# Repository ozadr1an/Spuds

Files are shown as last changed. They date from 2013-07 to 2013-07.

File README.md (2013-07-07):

Spuds
=====
**A Teensylu / Printrboard Mashup**
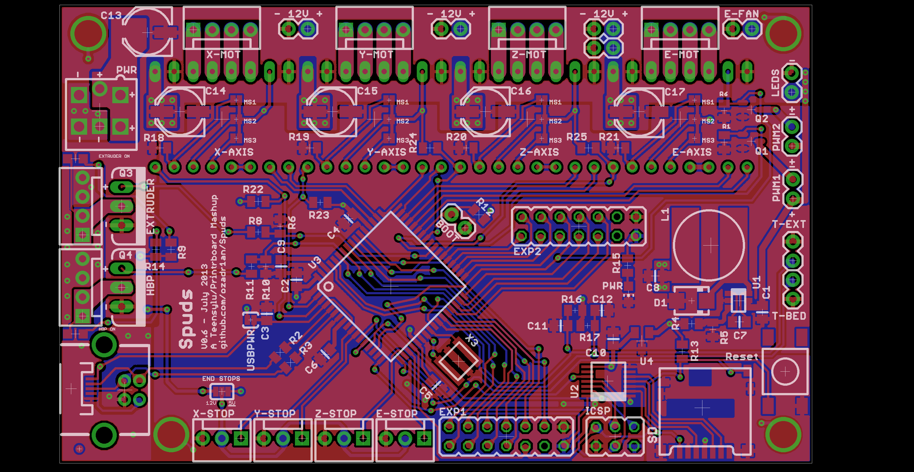
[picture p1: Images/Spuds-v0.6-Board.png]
Spuds-Board

Spuds was born from mashing together the concepts of both the Teensylu and Printrboard (itself a development of the Teensylu concept). The aim was to take the positives provided by the Printrboard design and incorporate some additions such as LED indicators on the MOSFETs, an additional PWM Fan header and an extra PWM Output header pin. It then reintroduced the modular Stepper Driver setup, as for many, the onboard Allegro drivers of the Printrboard are seen as a drawback as it limits options and replacement/repair. 

Spuds has expansion headers supporting I2C, SPI, UART, and ADC pins. All extra I/O ports of the AT90USB have been broken out to headers for prototyping and expansion. It follows the footprint for headers that the Printrboard introduced to allow compatibility with other expansions devices such as LCD's and the Extrudr board. 

The continued use of the AT90USB1286 used in the Teensylu and Printrboard means Spuds also has on-chip USB, removing the need for the FTDI UART (USB-to-serial) IC. On-chip USB means dramatically faster firmware upload times and communication. The AT90USB connects at any baud rate regardless of firmware configuration, and operates virtually free of serial communication errors/pauses.

This board is currently in pre-release design phases, so is subject to changes!

**Licence: _CC ShareAlike 3.0_**

**Attributions:**
* **_Teensylu_** (StephS 2011) http://reprap.org/wiki/Teensylu
* **_Printrboard_** (Laine Walker-Avina 2012) http://reprap.org/wiki/Printrboard

##Features
* Small design - board is 100mm x 60mm (4" x 2.4")
* Atmel AT90USB1286 Microcontroller (or AT90USB1287 drop-in compatible for 20mhz support)
 * Native USB interface. No FTDI serial-to-USB chip.
 * 128kb Flash
* Modular Stepper Driver Support (Add/Replace as needed)
* Solder Jumper Microstepping Selection
* Thermistor Connectivity: 2
* N-MOSFETs for Extruder and Heatbed control
 * LED Status Indicators for Power, HBP and Extruder (Troubleshooting, PID Monitoring)
* 2 N-MOSFET for low power Fan or motor
* 6 2-Pin Header 12V Connections for additional features such as LEDs, Cooling Fans, etc
* Onboard SD card slot
* Four Endstop connectors 
 * User selectable via Solder Jumpers 5V or 12v Rails.
 * Includes X, Y, Z, and fourth endstop called E-Stop to be used as an emergency stop, or extruder stop (to be added in firmware).
* Supports multiple power configurations (Carried from Sanguinololu)
 * Logic & Motors supplied by ATX or laptop power supply (12-20V 120W minimum)
 * Logic supplied by USB bus (if enabled by solder jumper)
 * Logic supplied by on-board voltage regulator
 * On-board USB connectivity
* Edge connectors enabling use of vertical or right-angle connections
* 15 Extra pins available for expansion and development, with the following capabilities
 * UART1 (RX and TX)
 * I2C (SDA and SCL)
 * SPI (MOSI, MISO, SCK)
 * PWM pin (2)
 * Analog I/O (6)
 * JTAG (uses some of the ADC pins)
 * Additional 14 pin header with remaining I/O for prototyping
 * SMT Components sized at 0805, and no QFNs for easier soldering.
 * 2-Layer PCB to reduce manufacture cost & complexity

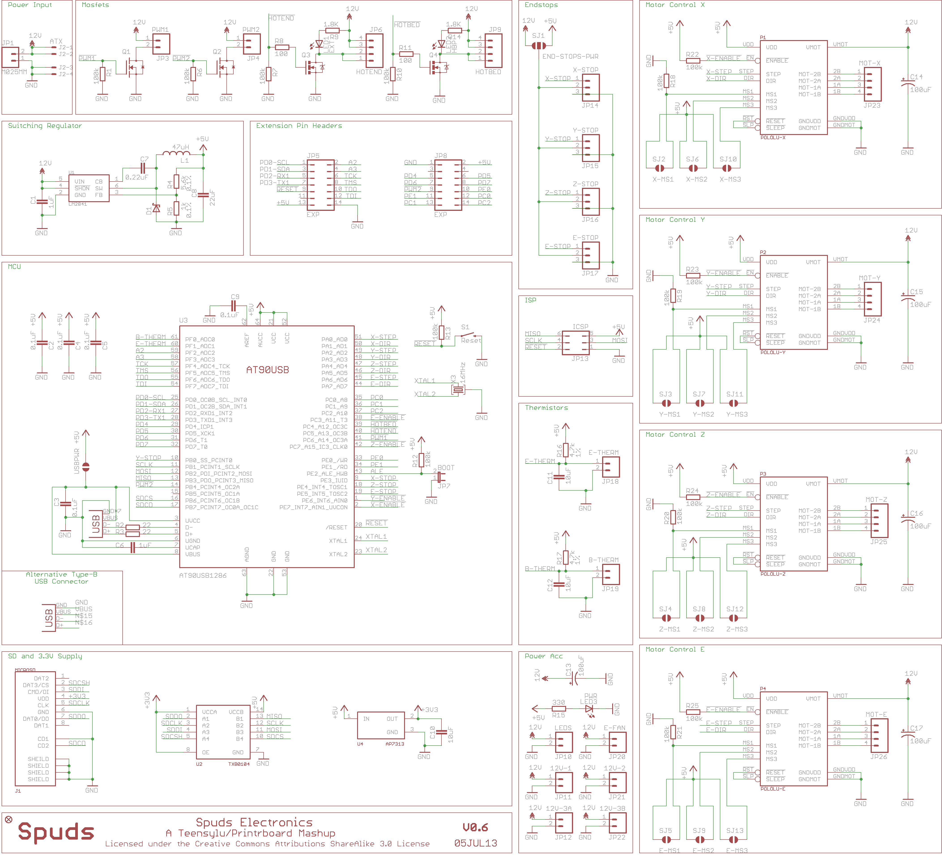
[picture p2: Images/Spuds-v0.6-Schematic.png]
Spuds-Schematic


####Benefits of this Design
* Allows modular use of Stepper Drivers, allowing:
 * User selection of driver used
 * The re-use of existing drivers
 * Replacement due to fault/failure.

* Integrated USB controller provides 12MBps bandwidth, instead of usual slower serial comms via FTDI. Result: Virtually no serial communication errors and interruptions due to PC Activity reduced.
* Integrated micro-SD Card slot
* Uses small standard Molex connectors for motors, heater, and endstops.

####Bill of Materials
Available via [GoogleDocs](https://docs.google.com/spreadsheet/ccc?key=0ArIeeziM0bp9dG5TbjlYaFVDQ0I5dkZXbHk2VjhtQlE&usp=sharing)

####Revision History
* V0.5 [July 2013]: Internal pre-production design.

####Compatible Firmwares
* Sprinter: http://reprap.org/wiki/Sprinter
* Marlin: No official support yet, but works with Lincomatic's fork (https://github.com/lincomatic/Marlin) or the Unofficial Solidoodle Firmware (https://github.com/mlaws/solidoodle2-marlin)
* Repetier List_of_Firmware#Repetier-Firmware: Supported, use MOTHERBOARD == 8. (https://github.com/repetier/Repetier-Firmware)
* grbl: No official support yet, but works with Lincomatic's fork. (http://blog.lincomatic.com/?p=564)

(Other firmwares are currently untested but any firmware for an arduino mega should work with proper pin setup.)

####Alternate Bootloader
If you have an ISP or JTAG cable, you can also program an alternate bootloader from the LUFA project that allows you to potentially program with the standard Arduino software.
* Download BootloaderCDC.zip
* Unzip to get BootloaderCDC.hex
* Program using your favorite ISP/JTAG cable.
 * The command for avrdude is avrdude -p at90usb1286 -c <your programmer here> -U flash:w:BootloaderCDC.hex

###Setup
####Stepper Motors
Connect the X, Y, Z axis, and extruder motors to the matching headers at the top of the Printrboard (X-MOT, Y-MOT, Z-MOT, E-MOT). Headers are 4 wire Molex KK series, part# 0022013047) with 2759 series crimp terminals, part# 0008550101. Motor pinout is:
1. A - Phase 1+
2. B - Phase 1-
3. C - Phase 2+
4. D - Phase 2-

####Endstops
Connect mechanical microswitches to the 3-pin Molex headers X-STOP, Y-STOP, Z-STOP at the bottom of the board. E-STOP is reserved for future use. Connect switches as follows:
#####Standard Microswitches
1. Switch NC
2. No connection
3. Switch COMMON

#####For optos:
1. Signal Output
2. +5V or +12V
3. GND

####Heaters
* LEDs are fitted to indicate when the MOSFET is active. These can be ommitted if desired. 
* Connect the heating element of your hotend (resistor or nichrome wire) to the 4-pin EXTRUDER header, positioned next to MOSFET Q1. 
* Connect your heatbed to the HOTBED header, next to MOSFET Q2. Polarity here is unimportant; pinout is as follows:

1. Positive
2. Positive
3. Negative
4. Negative

####Thermistors
Thermistor headers are 2-pin Molex headers at the right side of the board, located above the reset button.
* Connect the HBP thermistor to the header directly above the reset button. 
* The Extruder thermistor also connects above the reset button next to the HBP thermistor.

####Low Power Fan
A 2-pin Molex header labelled FAN is located on the right side of the board, above the thermistor headers. 
* This optional header can be used to power a fan or other small motor.

####Board Power
All power is supplied through a choice of connector at the upper left corner of the Spuds, labelled PWR:
* 4-pin ATX style header (Suitable for high current HBP)
* 5.08mm 2-Pin Screw Terminal (Suitable for low current HBP only)

Connect directly to any 12VDC power supply. 
* Ground terminals are closest to the edge of the board
* 12VDC+ terminals are located behind.

####USB
Choice of USB Connector (only one can be installed). The Type-B connector is a good choice for long cable runs, as you can easily acquire heavily sheilded thick gauge USB cables as used for Printers. Micro-USB is perhaps a good choice if a small compact connection is required, or for interconnection to another controller system such as a tablet or RPi:
* Micro-USB B Connector
* Type-B USB Connector

**Note that a jumper should _NOT_ be installed on the "BOOT" pins for normal operation (see _Bootloaders_ ).**

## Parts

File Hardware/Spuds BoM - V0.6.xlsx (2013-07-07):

Qty | Value | Device | Board Ref. | Digikey p/n | Unit Price | Total Part Price
1 | TXB0104 | TXB0104 Bi-Di Level Translator | U2 | 296-21929-1-ND | 0.743 | $0.74
1 | AP7313 | AP7313 3.3V LDO SOT-23 | U4 | AP7313-33SAG-7DICT-ND | 0.112 | $0.11
1 | AT90USB1286-AU | AT90USB | U3 | AT90USB1286-AURCT-ND | 6.14 | $6.14
1 | LM2841 | LM2841 Switching Regulator | U1 | LM2841XMK-ADJLCT-ND | 1.596 | $1.60
1 | BOOT | 0.1” 2-PIN MALE HEADER | JP7 | WM4000-ND | 0.063 | $0.06
2 | EXP | 0.1” 2X7 MALE PIN HEADER | JP5, JP8 | 609-3491-ND | 0.14166 | $0.28
1 | ICSP | 0.1” 2X3 MALE PIN HEADER | JP13 | 609-3210-ND | 0.29275 | $0.29
7 | LEDS/12V | 0.1” 2-PIN MALE HEADER | JP3, JP4, JP11, JP21, JP12, JP22, JP20 | WM4000-ND | 0.063 | $0.44
6 | MOTOR | 4-PIN 0.1” POLARIZED MOLEX KK-SERIES | JP6, JP9, JP23, JP24, JP25, JP26 | WM4113-ND | 0.17596 | $1.06
2 | THERM | 2-PIN 0.1” POLARIZED MOLEX KK-SERIES | JP18, JP19 | WM4111-ND | 0.09237 | $0.18
4 | ENDSTOP | 3-PIN 0.1” POLARIZED MOLEX KK-SERIES | JP14, JP15, JP16, JP17 | WM4112-ND | 0.13541 | $0.54
2 | POLOLU-SOCKET | CONN HEADER 32POS SOCKET 2.54MM |  | 732-2860-ND | 1.34 | $2.68
1 | MICROSD | MICROSD Socket, Amphenol | J1 | 114-00841-68-1-ND | 0.856 | $0.86
1 | USB-PTH-B | CONN USB TYPE B R/A BLACK | X2 | ED2983-ND | 0.54 | $0.54
0 | USB-MICROB | USB-MICROB | X1 | 455-2562-1-ND | 0.5355 | $0.00
0 | PWR | TERM BLOCK 2POS SIDE ENTRY 5MM | JP1 | A98355-ND | 0.87 | $0.00
1 | ATX | Molex Mini-Fit Jr. 5566-4 | J3 | WM3801-ND | 0.33582 | $0.34
1 | 20MHz | RESONATOR W/ INTEGRATED CAP | X3 | 535-10011-1-ND | 0.45 | $0.45
0 | 16MHz | RESONATOR W/ INTEGRATED CAP | X3 | 535-10008-2-ND | 0.182 | $0.00
5 | 0.1uF | CAPACITOR CERAMIC 0805 | C2, C3, C4, C5, C9 | 311-1361-1-ND | 0.006 | $0.03
1 | 0.22uF | CAPACITOR CERAMIC 0805 | C7 | 399-3491-1-ND | 0.02043 | $0.02
2 | 1uF | CAPACITOR CERAMIC 0805 | C1, C6 | 587-2229-1-ND | 0.03055 | $0.06
3 | 10uF | CAPACITOR CERAMIC 0805 | C10, C11, C12 | 311-1355-1-ND | 0.025 | $0.07
1 | 22uF | CAPACITOR CERAMIC 0805 | C8 | 587-1305-1-ND | 0.056 | $0.06
5 | 100uF | CAP, Al Electrolytic, Panasonic-D Pkg | C13, C14, C15, C16, C17 | PCE3951CT-ND | 0.1202 | $0.60
1 |  | DIODE SCHOTTKY 40V 1A SMA | D1 | B140-FDICT-ND | 0.0648 | $0.06
1 | 47uH | Inductor, SMT 1.25A | L1 | SDR1006-470KLCT-ND | 0.3 | $0.30
3 | PWR | LED GREEN 0805 | LED1, LED2, LED3 | 754-1131-1-ND | 0.039 | $0.12
2 |  | Logic-level n-Chan MOSFET SOT-23 | Q1, Q2 | IRLML2060TRPBFCT-ND | 0.087 | $0.17
2 |  | Logic-level n-Chan MOSFET TO-220 | Q3, Q4 | IRLB8743PBF-ND | 0.52632 | $1.05
1 | 1k | RESISTOR_0805 0.1% | R5 | RG20P1.0KBCT-ND | 0.058 | $0.06
2 | 1.8k | RESISTOR_0805 | R9, R14 | 311-1.8LHCT-ND | 0.058 | $0.12
2 | 4.7k | RESISTOR_0805 1% | R16, R17 | 311-4.70KCRCT-ND | 0.00266 | $0.01
1 | 5.6k | RESISTOR_0805 0.1% | R4 | P5.6KDATR-ND | 0.013 | $0.01
2 | 22 | RESISTOR_0805 | R2, R3 | 311-22ARCT-ND | 0.00209 | $0.00418
2 | 100 | RESISTOR_0805 | R8, R11 | 311-100ARCT-ND | 0.00209 | $0.00418
14 | 100k | RESISTOR_0805 | R1, R6, R7, R10, R12, R13, R18, R19, R20, R21, R22, R23, R24, R25 | RMCF0805JT100KCT-ND | 0.0019 | $0.03
1 | 330 | RESISTOR_0805 | R15 | 311-330ARCT-ND | 0.00209 | $0.00209
1 | Reset | SWITCH-MOMENTARY-2 | S2 | 450-1133-ND | 0.1398 | $0.14
 |  |  |  |  | Total: | $19.24

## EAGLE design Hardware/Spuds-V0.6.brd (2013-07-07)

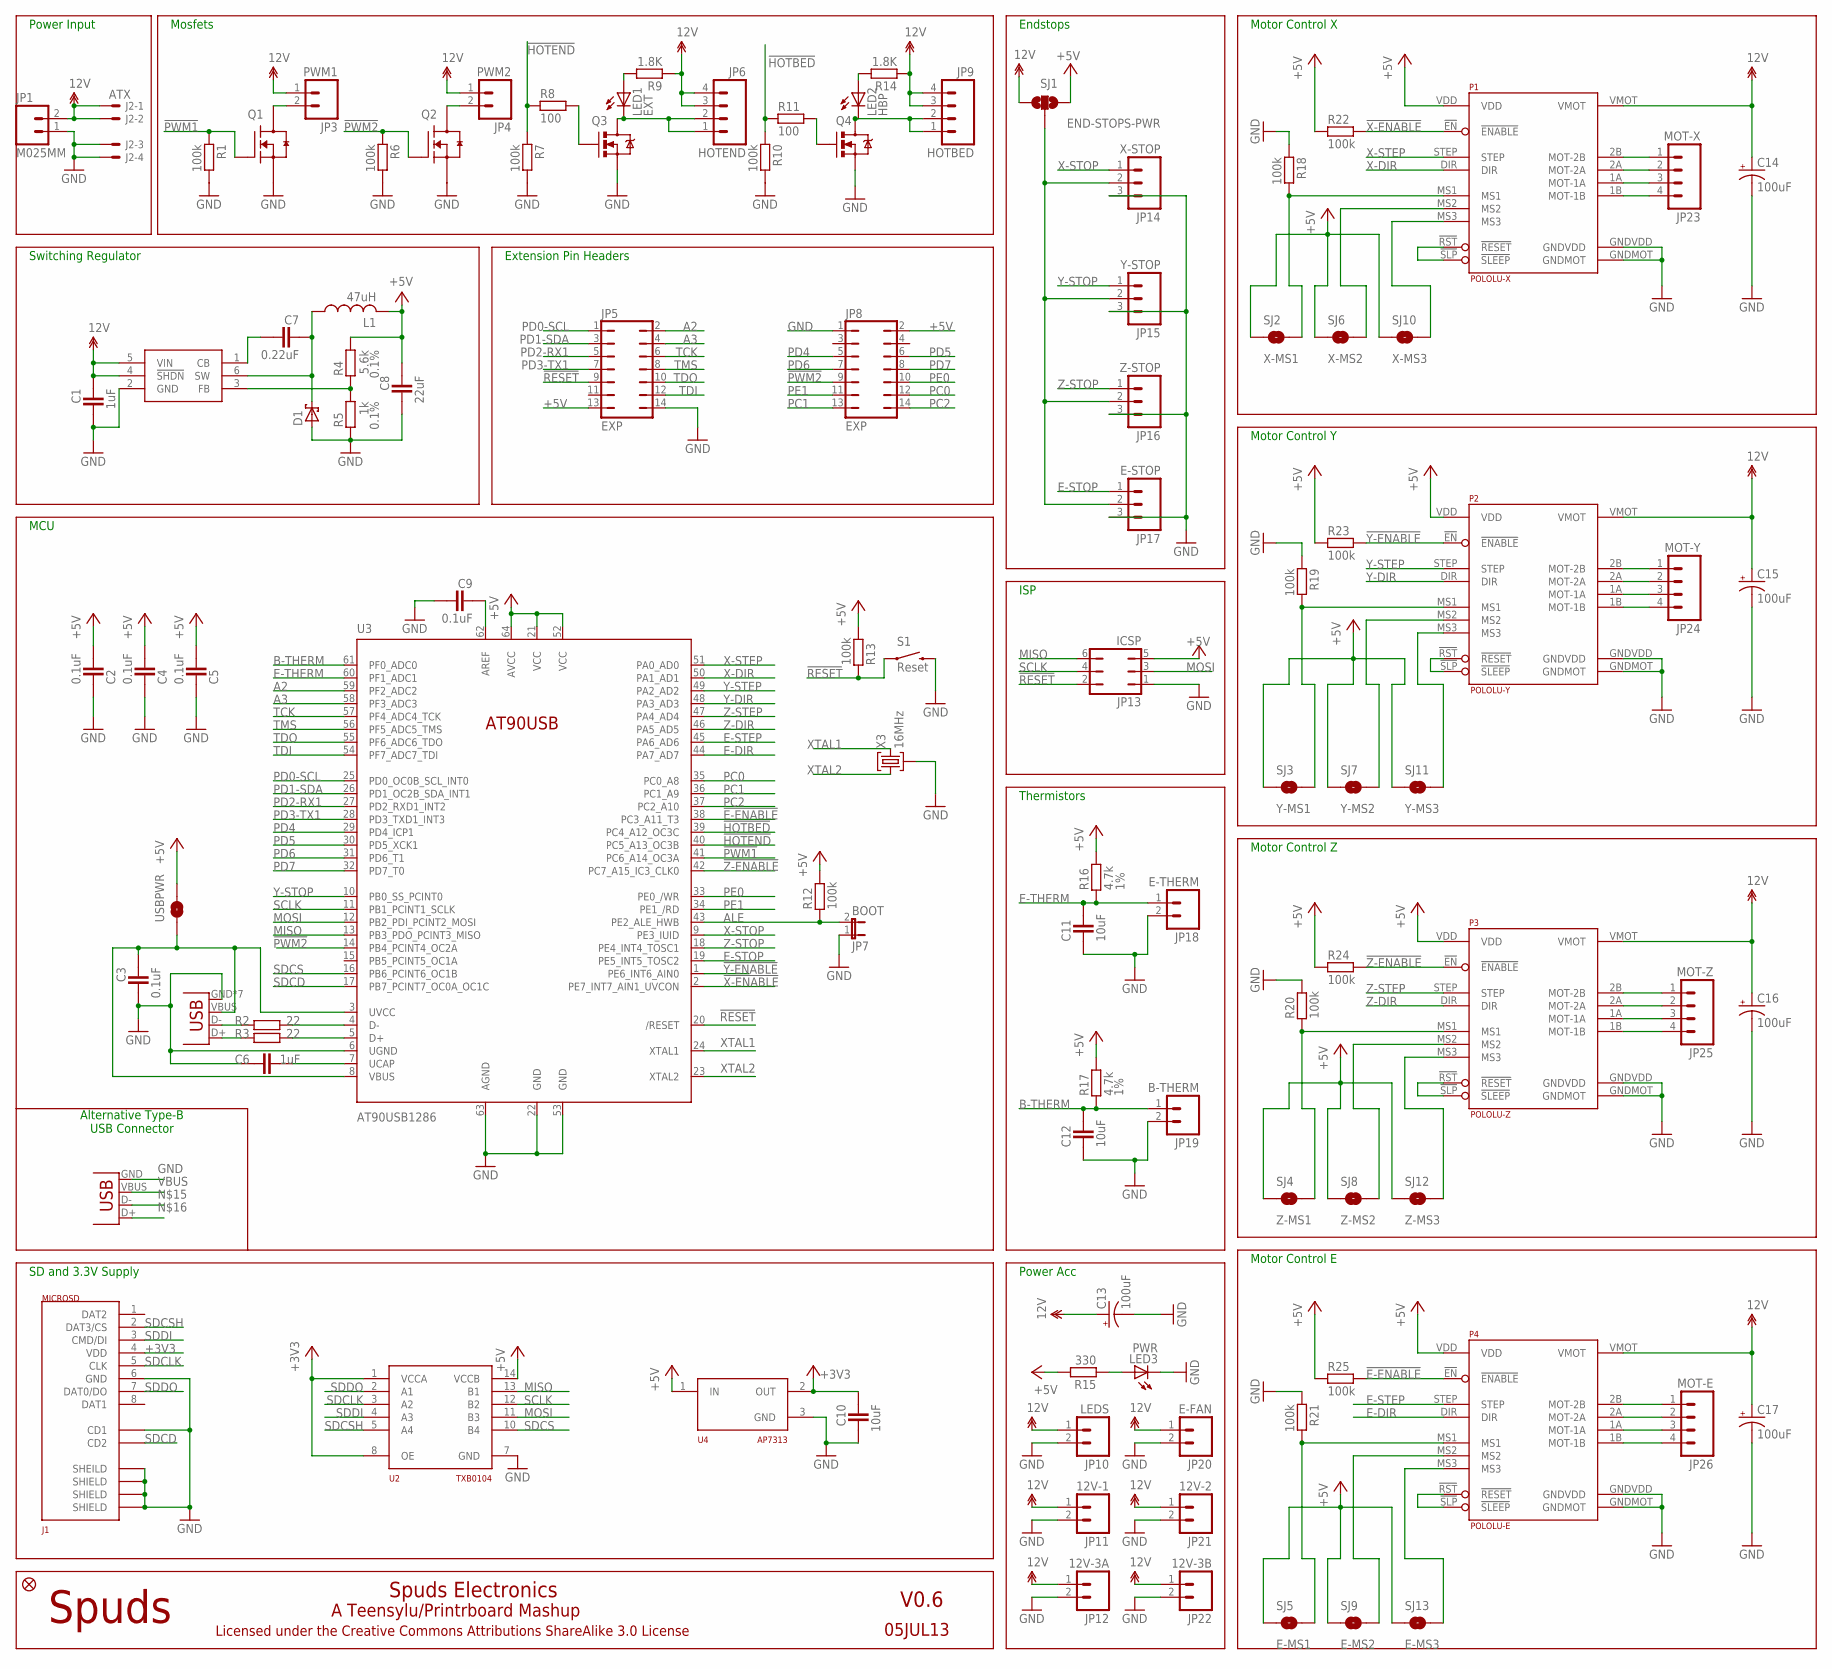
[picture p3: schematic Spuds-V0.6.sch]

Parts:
C1, C6: 1uF; CAPC2012X145AN; PARTNO 587-2229-1-ND
C2, C3, C4, C5, C9: 0.1uF; CAPC2012X145AN; PARTNO 311-1361-1-ND
C7: 0.22uF; CAPC2012X145AN; PARTNO 399-3491-1-ND
C8: 22uF; CAPC2012X145AN; PARTNO 587-1305-1-ND
C10, C11, C12: 10uF; CAPC2012X145AN; PARTNO 311-1355-1-ND
C13, C14, C15, C16, C17: 100uF; PANASONIC_D; PARTNO PCE3951CT-ND
D1: SCH-DIODESMA; SMA; PARTNO B140-FDICT-ND
J1: MICROSD; AMPHENOL-MICROSD; PARTNO ED2983-ND
J2: ATX; 5566-4; PARTNO WM3801-ND
JP1: M025MM; SCREWTERMINAL-5MM-2; PARTNO A98355-ND
JP2: FIDUCIAL1X2.5; FIDUCIAL-1X2.5; PARTNO *
JP3: PWM1; 1X02; PARTNO WM4000-ND
JP4: PWM2; 1X02; PARTNO WM4000-ND
JP5, JP8: EXP; JP7Q; PARTNO 609-3491-ND
JP6: HOTEND; MOLEX-1X4; PARTNO WM4113-ND
JP7: BOOT; 1X02; PARTNO WM4000-ND
JP9: HOTBED; MOLEX-1X4; PARTNO WM4113-ND
JP10: LEDS; 1X02; PARTNO WM4000-ND
JP11: 12V-1; 1X02; PARTNO WM4111-ND
JP12: 12V-3A; 1X02; PARTNO WM4111-ND
JP13: ICSP; JP3Q; PARTNO 609-3210-ND
JP14: X-STOP; MOLEX-1X3; PARTNO WM4112-ND
JP15: Y-STOP; MOLEX-1X3; PARTNO WM4112-ND
JP16: Z-STOP; MOLEX-1X3; PARTNO WM4112-ND
JP17: E-STOP; MOLEX-1X3; PARTNO WM4112-ND
JP18: E-THERM; 1X02; PARTNO WM4111-ND
JP19: B-THERM; 1X02; PARTNO WM4111-ND
JP20: E-FAN; 1X02; PARTNO WM4111-ND
JP21: 12V-2; 1X02; PARTNO WM4111-ND
JP22: 12V-3B; 1X02; PARTNO WM4111-ND
JP23: MOT-X; MOLEX-1X4; PARTNO WM4113-ND
JP24: MOT-Y; MOLEX-1X4; PARTNO WM4113-ND
JP25: MOT-Z; MOLEX-1X4; PARTNO WM4113-ND
JP26: MOT-E; MOLEX-1X4; PARTNO WM4113-ND
L1: 47uH; SDR1006; PARTNO SDR1006-470KLCT-ND
LED1: EXT; CHIP-LED0805; PARTNO 754-1132-1-ND
LED2: HBP; CHIP-LED0805; PARTNO 754-1437-1-ND
LED3: PWR; CHIP-LED0805; PARTNO 754-1131-1-ND
P1: POLOLU-X; POLOLU-ALLEGRO-PTH; PARTNO 952-1823-ND
P2: POLOLU-Y; POLOLU-ALLEGRO-PTH; PARTNO 952-1823-ND
P3: POLOLU-Z; POLOLU-ALLEGRO-PTH; PARTNO 952-1823-ND
P4: POLOLU-E; POLOLU-ALLEGRO-PTH; PARTNO 952-1823-ND
Q1, Q2: RFP30N06LE; SOT95P280X135-3N; PARTNO IRLML2060TRPBFCT-ND
Q3, Q4: RFP30N06LE; TO220V; PARTNO IRLB8743PBF-ND
R1, R6, R7, R10, R12, R13, R18, R19, R20, R21, R22, R23, R24, R25: 100k; RESC2012X70N; PARTNO RMCF0805JT100KCT-ND
R2, R3: 22; RESC2012X70N; PARTNO 311-22ARCT-ND
R4: 5.6k; RESC2012X70N; TOLERANCE 0.1%; PARTNO P5.6KDATR-ND
R5: 1k; RESC2012X70N; TOLERANCE 0.1%; PARTNO RG20P1.0KBCT-ND
R8, R11: 100; RESC2012X70N; PARTNO 311-100ARCT-ND
R9, R14: 1.8K; RESC2012X70N; PARTNO 311-1.8LHCT-ND
R15: 330; RESC2012X70N; PARTNO 311-330ARCT-ND
R16, R17: 4.7k; RESC2012X70N; TOLERANCE 1%; PARTNO 311-4.70KCRCT-ND
S1: Reset; TACTILE_SWITCH_TALL; PARTNO 450-1133-ND
SJ1: END-STOPS-PWR; SJ_3_PASTE2&3; PARTNO *
SJ2: X-MS1; SJ_2S; PARTNO *
SJ3: Y-MS1; SJ_2S; PARTNO *
SJ4: Z-MS1; SJ_2S; PARTNO *
SJ5: E-MS1; SJ_2S; PARTNO *
SJ6: X-MS2; SJ_2S; PARTNO *
SJ7: Y-MS2; SJ_2S; PARTNO *
SJ8: Z-MS2; SJ_2S; PARTNO *
SJ9: E-MS2; SJ_2S; PARTNO *
SJ10: X-MS3; SJ_2S; PARTNO *
SJ11: Y-MS3; SJ_2S; PARTNO *
SJ12: Z-MS3; SJ_2S; PARTNO *
SJ13: E-MS3; SJ_2S; PARTNO *
U1: LM2841; TSOT6; PARTNO LM2841XMK-ADJLCT-ND
U2: TXB0104; TSSOP14; PARTNO 296-21929-1-ND
U3: AT90USB1286; TQFP64-2; PARTNO AT90USB1286-AURCT-ND
U4: AP7313; SOT23C; PARTNO AP7313-33SAG-7DICT-ND
USBPWR: SOLDERJUMPERNO; SJ_2S-NO; PARTNO *
X1: USBPTH; USB-B-PTH; PARTNO ED2983-ND
X2: USB-MICROB; PARTNO 455-2562-1-ND
X3: 16MHz; AWSCR; PARTNO 535-10011-1-ND

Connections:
12V: C1.1, C13.+, C14.+, C15.+, C16.+, C17.+, J2.1, J2.2, JP1.2, JP3.1, JP4.1, JP6.3, JP6.4, JP9.3, JP9.4, JP10.1, JP11.1, JP12.1, JP20.1, JP21.1, JP22.1, P1.VMOT, P2.VMOT, P3.VMOT, P4.VMOT, R9.1, R14.1, SJ1.1, U1.4 (!SHDN), U1.5 (VIN)
!E-ENABLE: P4.!EN (!ENABLE), R25.2, U3.38 (PC3_A11_T3)
!HOTBED: R10.1, R11.1, U3.39 (PC4_A12_OC3C)
!HOTEND: R7.1, R8.1, U3.40 (PC5_A13_OC3B)
!PWM1: Q1.1 (G), R1.1, U3.41 (PC6_A14_OC3A)
!PWM2: JP8.9, Q2.1 (G), R6.1, U3.14 (PB4_PCINT4_OC2A)
!RESET: JP5.9, JP13.2, R13.1, S1.A2 (1), U3.20 (/RESET)
!X-ENABLE: P1.!EN (!ENABLE), R22.2, U3.2 (PE7_INT7_AIN1_UVCON)
!Y-ENABLE: P2.!EN (!ENABLE), R23.2, U3.1 (PE6_INT6_AIN0)
!Z-ENABLE: P3.!EN (!ENABLE), R24.2, U3.42 (PC7_A15_IC3_CLK0)
+3V3: C10.1, J1.4 (VDD), U2.1 (VCCA), U2.8 (OE), U4.2 (OUT)
+5V: C2.2, C4.2, C5.2, C8.1, JP5.13, JP8.2, JP13.5, L1.P$2 (2), P1.VDD, P2.VDD, P3.VDD, P4.VDD, R4.1, R12.2, R13.2, R15.2, R16.2, R17.2, R22.1, R23.1, R24.1, R25.1, SJ1.3, SJ2.1, SJ3.1, SJ4.1, SJ5.1, SJ6.1, SJ7.1, SJ8.1, SJ9.1, SJ10.1, SJ11.1, SJ12.1, SJ13.1, U2.14 (VCCB), U3.21 (VCC), U3.52 (VCC), U3.64 (AVCC), U4.1 (IN), USBPWR.2
A2: JP5.2, U3.59 (PF2_ADC2)
A3: JP5.4, U3.58 (PF3_ADC3)
ALE: JP7.2, R12.1, U3.43 (PE2_ALE_HWB)
AREF: C9.1, U3.62 (AREF)
B-THERM: C12.2, JP19.1, R17.1, U3.61 (PF0_ADC0)
E-DIR: P4.DIR, U3.44 (PA7_AD7)
E-MS1: P4.MS1, R21.2, SJ5.2
E-MS2: P4.MS2, SJ9.2
E-MS3: P4.MS3, SJ13.2
E-RESETSLEEP: P4.!RST (!RESET), P4.!SLP (!SLEEP)
E-STEP: P4.STEP, U3.45 (PA6_AD6)
E-STOP: JP17.1, U3.19 (PE5_INT5_TOSC2)
E-THERM: C11.2, JP18.1, R16.1, U3.60 (PF1_ADC1)
END-STOP-PWR: JP14.2, JP15.2, JP16.2, JP17.2, SJ1.2
GND: C1.2, C2.1, C3.2, C4.1, C5.1, C6.1, C8.2, C9.2, C10.2, C11.1, C12.1, C13.-, C14.-, C15.-, C16.-, C17.-, D1.A, J1.6 (GND), J1.C1 (SHEILD), J1.C2 (SHIELD), J1.C3 (SHIELD), J1.C4 (SHIELD), J1.CD1, J2.3, J2.4, JP1.1, JP5.14, JP7.1, JP8.1, JP10.2, JP11.2, JP12.2, JP13.1, JP14.3, JP15.3, JP16.3, JP17.3, JP18.2, JP19.2, JP20.2, JP21.2, JP22.2, LED3.C, P1.GNDMOT, P1.GNDVDD, P2.GNDMOT, P2.GNDVDD, P3.GNDMOT, P3.GNDVDD, P4.GNDMOT, P4.GNDVDD, Q1.2 (S), Q2.2 (S), Q3.3 (S), Q4.3 (S), R1.2, R5.2, R6.2, R7.2, R10.2, R18.1, R19.1, R20.2, R21.1, S1.B2 (2), U1.2 (GND), U2.7 (GND), U3.6 (UGND), U3.22 (GND), U3.53 (GND), U3.63 (AGND), U4.3 (GND), X1.GND, X2.GND, X2.MT1 (GND), X2.MT2 (GND), X2.MT3 (GND), X2.MT4 (GND), X2.MT5 (GND), X2.MT6 (GND), X3.GND (2)
HOTBED-GND: JP9.1, JP9.2, LED2.C, Q4.2 (D)
HOTEND-GND: JP6.1, JP6.2, LED1.C, Q3.2 (D)
MISO: JP13.6, U2.13 (B1), U3.13 (PB3_PDO_PCINT3_MISO)
MOSI: JP13.3, U2.11 (B3), U3.12 (PB2_PDI_PCINT2_MOSI)
unnamed: LED3.A, R15.1
unnamed: LED1.A, R9.2
unnamed: R2.2, U3.4 (D-)
unnamed: R3.2, U3.5 (D+)
unnamed: LED2.A, R14.2
unnamed: JP3.2, Q1.3 (D)
unnamed: Q4.1 (G), R11.2
unnamed: JP24.2, P2.2A (MOT-2A)
unnamed: C6.2, U3.7 (UCAP)
unnamed: JP23.1, P1.2B (MOT-2B)
unnamed: JP23.2, P1.2A (MOT-2A)
unnamed: JP23.3, P1.1A (MOT-1A)
unnamed: JP23.4, P1.1B (MOT-1B)
unnamed: JP4.2, Q2.3 (D)
unnamed: R2.1, X1.D-, X2.D-
unnamed: R3.1, X1.D+, X2.D+
unnamed: R4.2, R5.1, U1.3 (FB)
unnamed: JP24.3, P2.1A (MOT-1A)
unnamed: JP24.4, P2.1B (MOT-1B)
unnamed: JP24.1, P2.2B (MOT-2B)
unnamed: JP26.1, P4.2B (MOT-2B)
unnamed: JP26.2, P4.2A (MOT-2A)
unnamed: JP26.3, P4.1A (MOT-1A)
unnamed: JP26.4, P4.1B (MOT-1B)
unnamed: Q3.1 (G), R8.2
unnamed: C7.1, D1.C, L1.P$1 (1), U1.6 (SW)
unnamed: C7.2, U1.1 (CB)
PC0: JP8.12, U3.35 (PC0_A8)
PC1: JP8.13, U3.36 (PC1_A9)
PC2: JP8.14, U3.37 (PC2_A10)
PD0-SCL: JP5.1, U3.25 (PD0_OC0B_SCL_INT0)
PD1-SDA: JP5.3, U3.26 (PD1_OC2B_SDA_INT1)
PD2-RX1: JP5.5, U3.27 (PD2_RXD1_INT2)
PD3-TX1: JP5.7, U3.28 (PD3_TXD1_INT3)
PD4: JP8.5, U3.29 (PD4_ICP1)
PD5: JP8.6, U3.30 (PD5_XCK1)
PD6: JP8.7, U3.31 (PD6_T1)
PD7: JP8.8, U3.32 (PD7_T0)
PE0: JP8.10, U3.33 (PE0_/WR)
PE1: JP8.11, U3.34 (PE1_/RD)
SCLK: JP13.4, U2.12 (B2), U3.11 (PB1_PCINT1_SCLK)
SDCD: J1.CD2, U3.17 (PB7_PCINT7_OC0A_OC1C)
SDCLK: J1.5 (CLK), U2.3 (A2)
SDCS: U2.10 (B4), U3.16 (PB6_PCINT6_OC1B)
SDCSH: J1.2 (DAT3/CS), U2.5 (A4)
SDDI: J1.3 (CMD/DI), U2.4 (A3)
SDDO: J1.7 (DAT0/DO), U2.2 (A1)
TCK: JP5.6, U3.57 (PF4_ADC4_TCK)
TDI: JP5.12, U3.54 (PF7_ADC7_TDI)
TDO: JP5.10, U3.55 (PF6_ADC6_TDO)
TMS: JP5.8, U3.56 (PF5_ADC5_TMS)
VBUS: C3.1, U3.3 (UVCC), U3.8 (VBUS), USBPWR.1, X1.VBUS, X2.VBUS
X-DIR: P1.DIR, U3.50 (PA1_AD1)
X-MS1: P1.MS1, R18.2, SJ2.2
X-MS2: P1.MS2, SJ6.2
X-MS3: P1.MS3, SJ10.2
X-RESETSLEEP: P1.!RST (!RESET), P1.!SLP (!SLEEP)
X-STEP: P1.STEP, U3.51 (PA0_AD0)
X-STOP: JP14.1, U3.9 (PE3_IUID)
XTAL1: U3.24 (XTAL1), X3.IN (3)
XTAL2: U3.23 (XTAL2), X3.OUT (1)
Y-DIR: P2.DIR, U3.48 (PA3_AD3)
Y-MS1: P2.MS1, R19.2, SJ3.2
Y-MS2: P2.MS2, SJ7.2
Y-MS3: P2.MS3, SJ11.2
Y-RESETSLEEP: P2.!RST (!RESET), P2.!SLP (!SLEEP)
Y-STEP: P2.STEP, U3.49 (PA2_AD2)
Y-STOP: JP15.1, U3.10 (PB0_SS_PCINT0)
Z-DIR: P3.DIR, U3.46 (PA5_AD5)
Z-MOT-1A: JP25.3, P3.1A (MOT-1A)
Z-MOT-1B: JP25.4, P3.1B (MOT-1B)
Z-MOT-2A: JP25.2, P3.2A (MOT-2A)
Z-MOT-2B: JP25.1, P3.2B (MOT-2B)
Z-MS1: P3.MS1, R20.1, SJ4.2
Z-MS2: P3.MS2, SJ8.2
Z-MS3: P3.MS3, SJ12.2
Z-RESETSLEEP: P3.!RST (!RESET), P3.!SLP (!SLEEP)
Z-STEP: P3.STEP, U3.47 (PA4_AD4)
Z-STOP: JP16.1, U3.18 (PE4_INT4_TOSC1)

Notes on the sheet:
Motor Control X
Motor Control Y
Motor Control Z
Motor Control E
ISP
Thermistors
Endstops
Mosfets
Power Acc
Spuds
V0.6
Spuds Electronics
Licensed under the Creative Commons Attributions ShareAlike 3.0 License
Extension Pin Headers
Switching Regulator
A Teensylu/Printrboard Mashup
SD and 3.3V Supply
Power Input
MCU
Alternative Type-B USB Connector
05JUL13

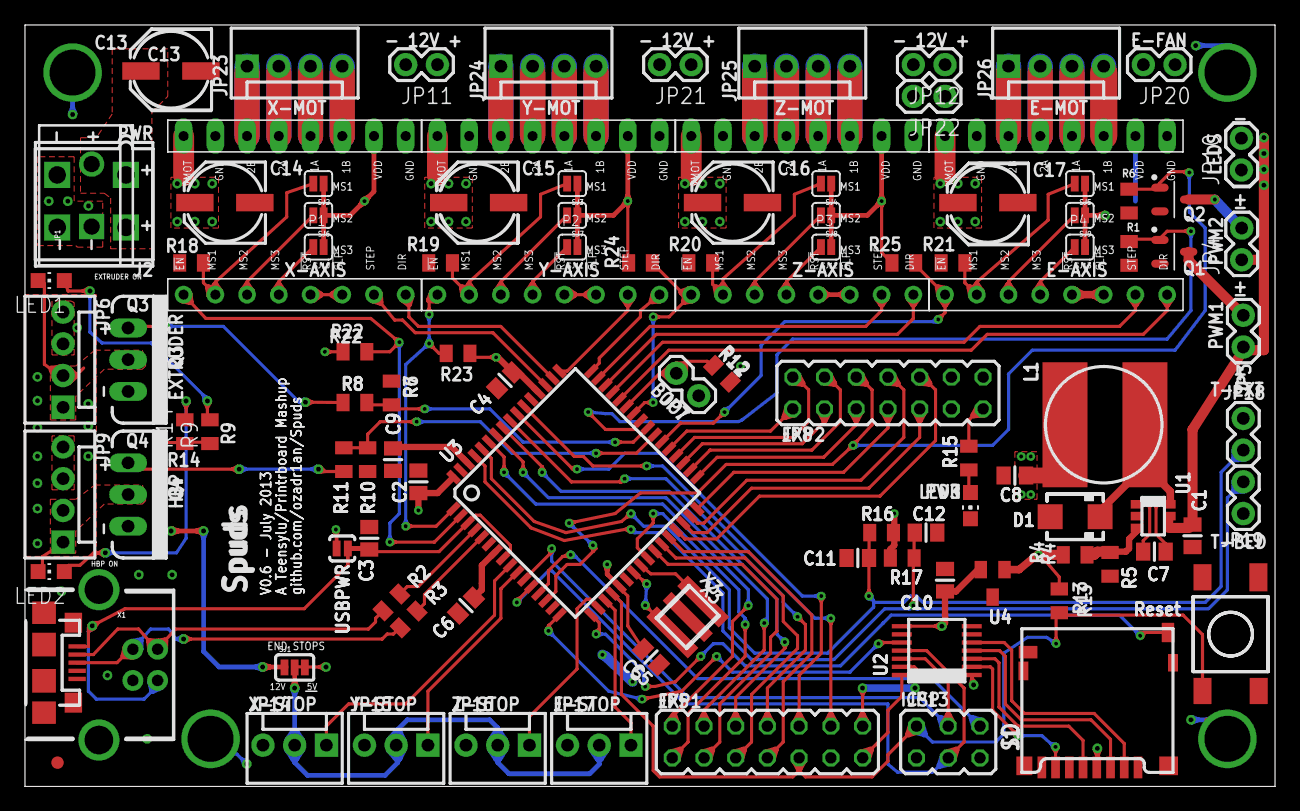
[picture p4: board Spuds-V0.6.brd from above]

Board: 4 copper layers, 100.1 x 61.0 mm, 106 parts (0 on the bottom side), 110 nets.

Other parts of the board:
DRILEGEND: DRILEGEND

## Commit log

2013-07-07 Initial Schematic/Board Commit V0.6 BoM
    [Spuds BoM - V0.6.xlsx, Spuds-V0.6.brd, Spuds-V0.6.sch]
2013-07-07 Update README.md
    Added Board/Schematic Images

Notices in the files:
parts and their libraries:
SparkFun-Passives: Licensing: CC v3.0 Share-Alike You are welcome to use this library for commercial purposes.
